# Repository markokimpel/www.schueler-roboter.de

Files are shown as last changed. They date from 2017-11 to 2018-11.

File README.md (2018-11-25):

---
permalink: /
---

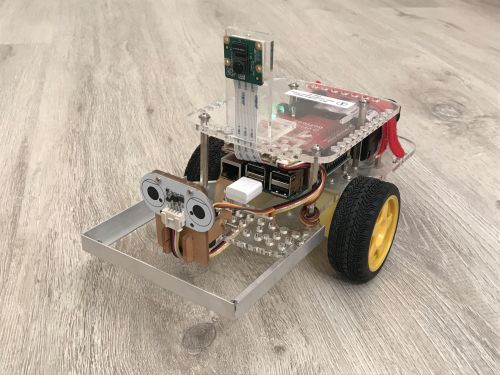
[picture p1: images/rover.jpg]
Schüler Roboter


* [Über das Projekt](project/)
* [News](news/)
  <ul>
    {% for post in site.posts %}
      <li>{{ post.date | date: "%d-%b-%Y" }} <a href="{{ post.url }}">{{ post.title }}</a></li>
      {% if forloop.index == 5 %}
        {% break %}
      {% endif %}
    {% endfor %}
  </ul>
* Anleitungen
  * [Bau des Roboters](tutorials/build_a_robot/)
  * [Basisinstallation Software](tutorials/software_image/)
  * [Programmieren mit Scratch](tutorials/programming_with_scratch/)
  * [Bilderkennung mit OpenCV](tutorials/image_recognition_with_opencv/)
* [Kontakt](contact/)

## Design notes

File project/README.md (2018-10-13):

---
title: Über das Projekt
permalink: /project/
breadcrumb_path: home
---

## Vision

Schaffung einer offenen und leistungsstarken Plattform auf der Schüler jeden Alters mit Freunde Computerkenntnisse erwerben können.

## Der Schüler-Roboter ist ein fahrbarer Roboter auf Basis des Raspberry Pis

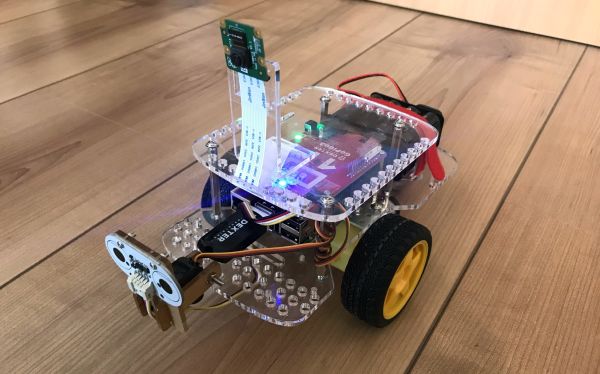
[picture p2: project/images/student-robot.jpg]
Schüler-Roboter


[Physical Computing](https://de.wikipedia.org/wiki/Physical_Computing) macht einfach mehr Spaß als das trockene Programmieren am Computer. Wir Menschen können leichter eine Verbindnung zu physischen Objekten aufbauen als zu abstrakten Aufgabenstellungen. Zielstellungen wie *Ding beweg dich* oder *mach' dies und das* ergeben sich bei physischen Objekten natürlich, ohne dass es einer zusätzlichen Motivation bedarf. Ein **selbstfahrender Roboter** erscheint hier als ideale Hardwarebasis.

Ein Raspberry Pi ist das Herzstück des Roboters. Der [Raspberry Pi 3 Model B](https://www.raspberrypi.org/products/raspberry-pi-3-model-b/) der Raspberry Pi Foundation ist ein leistungsstarker und kostengünstiger Einplatinenrechner. Seine offene Architektur erlaubt es verschiedene Betriebssysteme und Softwarepakete auf ihm laufen zu lassen und ihn mit verschiedenster Hardware zu integrieren. Seine große Beliebtheit im akademischen und Hobbybereich hat zu einer sehr aktiven Community und einem umfangreichen Angebot an Erweiterungen und Anleitungen geführt. Wir wählten den Raspberry Pi 3 Model B, da er ein **sehr breites Spektrum von Anwendungen** ermöglicht - von der Ansteuerung einzelner Komponenten (Motor an/aus), über die Programmierung mit Standardprogrammiersprachen wie Python, JavaScript und Java, die Nutzung von Roboterbetriebssystemen, bis zur Bilderkennung und künstlichen Intelligenz.

Als Hardwarebasis für den Roboter wird der [GoPiGo3](https://www.dexterindustries.com/gopigo3/) genutzt. Der GoPiGo3 ist einer der besten Roboter-Bausätze für den Raspberry Pi. Er enthält das Fahrgestell, die Motoren, Räder, die Steuerplatine, Stromversorgung, etc. Ein schwenkbarer Abstandssensor und eine leistungsstarke Kamera runden das Hardwarepaket ab.

## Ein sicherer Pfad durch den Jungle

Das umfangreiche und teilweise unübersichtliche Angebot an Komponenten und Software rund um den Raspberry Pi macht es dem Einsteiger bisweilen schwer geeignete und zueinander passende Komponenten auszuwählen und in ersten eigenen Projekten zu nutzen. Diese Hürde wird durch die **genaue Vorgabe von Komponenten** und **detailierten Anweisungen** genommen. Mit diesen erreichst du - mit Hilfe eines Kursleiters, Lehrers oder deiner Eltern - sicher das Ziel einen programmierbaren Roboters zu erschaffen. Die Programmierkurse sind auf diese Hardwarekomponenten abgestimmt. Von dem vorgegebenen Modell ausgehend können eigene Umbauten und Erweiterungen vorgenommen werden. Die Vielzahl der Projekte in der Community laden geradezu dazu ein.

## Einfach bis Rocket Science

Der Schüler-Roboter hat für jeden Schwierigkeitsgrad was zu bieten. Er eignet sich für Einsteiger, z.B. zum Erlernen der Programmierung mit der graphischen Programmiersprache Scratch. Er kann zum Erlernen von textuellen Programmiersprachen, wie z.B. Python, genutzt werden. Oder man taucht ein in die Bilderkennung und künstliche Intelligenz und lässt die neuesten Algorithmen auf ihm laufen.

## Alleine lernen oder in der Gruppe

Gerne kannst du dich allein durch die Anleitungen arbeiten. Oder du kommst du einer Veranstaltung. Interesse an einer massgeschneiderten Veranstaltung, z.B. für eine Schule? Bitte nehmen Sie [Kontakt](../contact/) mit uns auf.

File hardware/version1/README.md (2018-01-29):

[Hardware](..)

# Version 1

Version 1 nutzt ein selbstgedrucktes Chassis. Hierfür konnten wir freundlicherweise einen 3D Drucker der [Lichtwerkstatt](http://www.acp.uni-jena.de/lichtwerkstatt.html) des Abbe Center of Photonics nutzen. Es wird das gleiche Driver Board wie bei [Version 0](../version0/) verwendet. Die meisten der Kritikpunkte der Version 0 wurden durch die Eigenkonstruktion beseitigt. Zusätzlich wurde eine Kamera vorgesehen.

## Komponenten

Wir wählten folgende Komponenten:

Komponente | Bezug / Preis
-----------|------------
[Raspberry Pi 3 Model B](https://www.raspberrypi.org/products/raspberry-pi-3-model-b/) | [Amazon](https://www.amazon.de/gp/product/B01CD5VC92/) (ca. 35 €)
[Raspberry Pi Netzteil](https://www.raspberrypi.org/products/raspberry-pi-universal-power-supply/) | [Amazon](https://www.amazon.de/Raspberry-Offizielles-Pi-Netzteil-schwarz/dp/B01DP8O5A4/) (ca. 13 €)
32 GB microSD Karte mit Adapter<br/>(Kompatibilität mit Raspberry Pi beachten) | [Amazon](https://www.amazon.de/gp/product/B073JWXGNT/) (ca. 17 €)
[RapPiRobot Board V3](https://www.monkmakes.com/rrb3/) | (TODO)
[Raspberry Kamera](https://www.raspberrypi.org/products/camera-module-v2/) | (TODO)
2 Motoren und Räder | (TODO)
Nachlaufrad | (TODO)
2 Hülsen | (TODO)
3 Ultraschallsensoren | (TODO)
Steckbrett 400 Kontakte | (TODO)
Schrauben und Muttern | (TODO)
verschiedene Kabel | (TODO)
Batteriehalterung | (TODO)
6 AA Ni-MH Akkus mit hoher Kapazität | [Amazon](https://www.amazon.de/gp/product/B00JVV8HRW/) (2x ca. 12 €)
Ladegerät für AA Ni-MH Akkus | bereits vorhanden
**Gesamt** | **(TODO)**

PS: Die Auswahl der Komponenten basiert auf persönlichen Erfahrungen und Präferenzen. Bezugsquellen und Preise werden nur beispielhaft angegeben. Wir haben von keinem Hersteller oder Händler Vergünstigungen - jeglicher Art - für die Auswahl oder das Verlinken der Produkte erhalten.

## 3D Modell

* [Hauptplatte](3d_model/SR1%20Base%20Plate%20Rev%203.stl)
* [Raspberryhalterung](3d_model/SR1%20Raspberry%20Socket%20Rev%203.stl) (basiert auf [Raspberry Pi Case - HifiBerry Dac+](https://www.thingiverse.com/thing:2325301) von B_Dubb, veröffentlicht am 16. May 2017)
* [Abstandshalter Raspberryhalterung](3d_model/SR1%20Raspberry%20Socket%20Spacers%20Rev%201.stl)
* [Motorhalterung rechts](3d_model/SR1%20Motor%20Bracket%20R%20Rev%204.stl)
* [Motorhalterung links](3d_model/SR1%20Motor%20Bracket%20L%20Rev%204.stl)
* [Ultraschallsensorhalterung](3d_model/SR1%20Sonar%20Bracket%20Rev%202.stl) (3x benötigt)
* [Käfig mit Kamerahalterung](3d_model/SR1%20Cage%20Rev%200.stl)

Gedruckt wurde mit einem Prusa i3 MK2S, PLA, 200 µm.

## Fotos

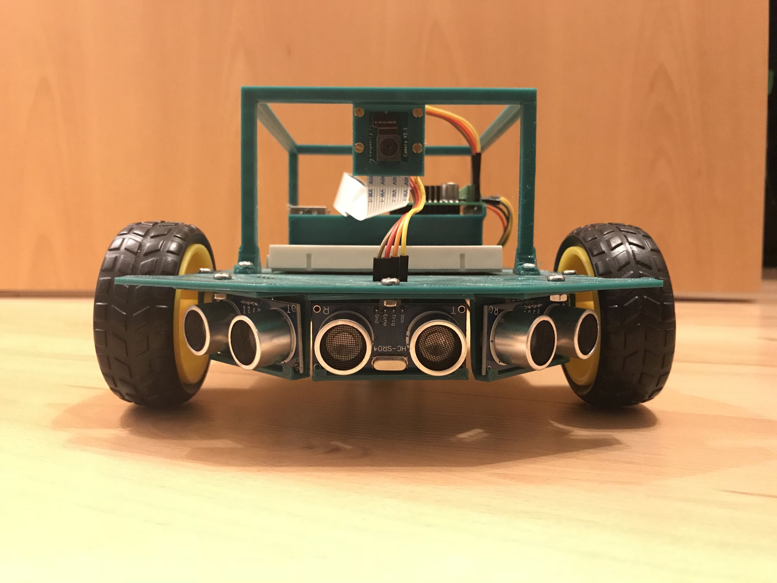
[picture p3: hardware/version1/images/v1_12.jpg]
vorn

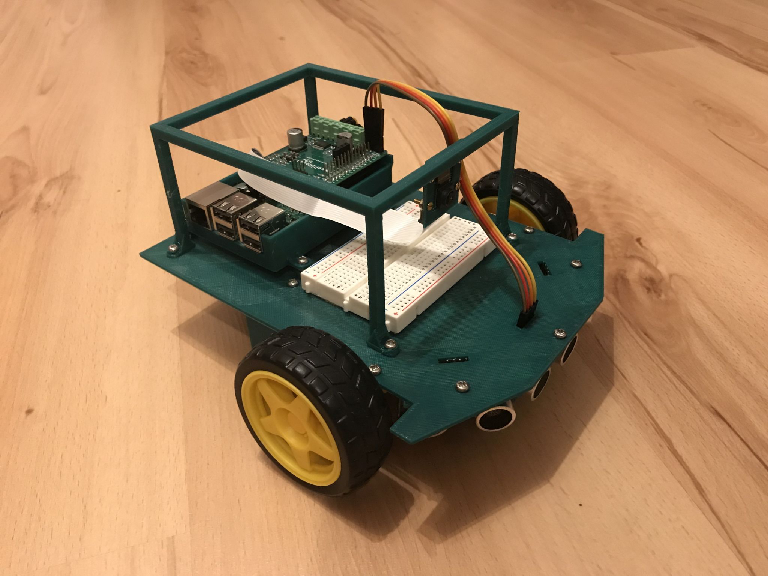
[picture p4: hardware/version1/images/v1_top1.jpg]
rechts

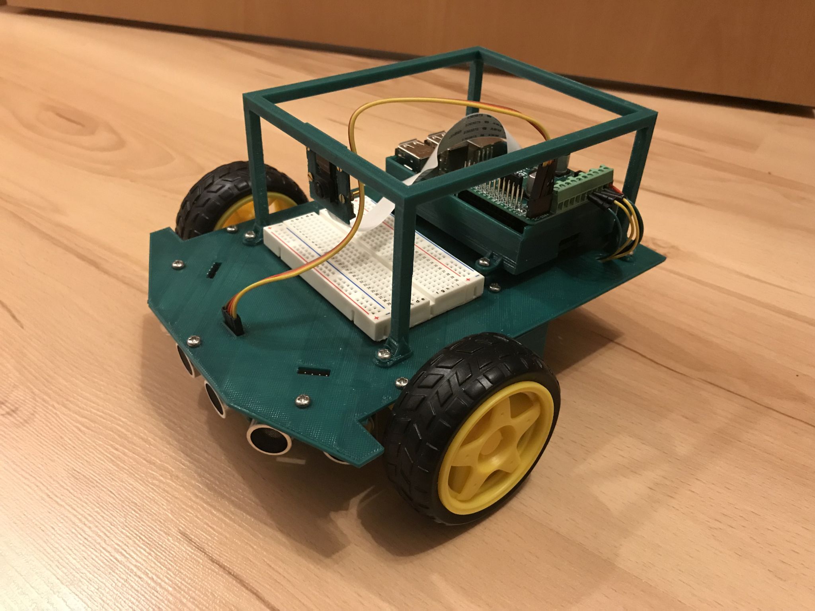
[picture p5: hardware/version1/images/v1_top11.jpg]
links

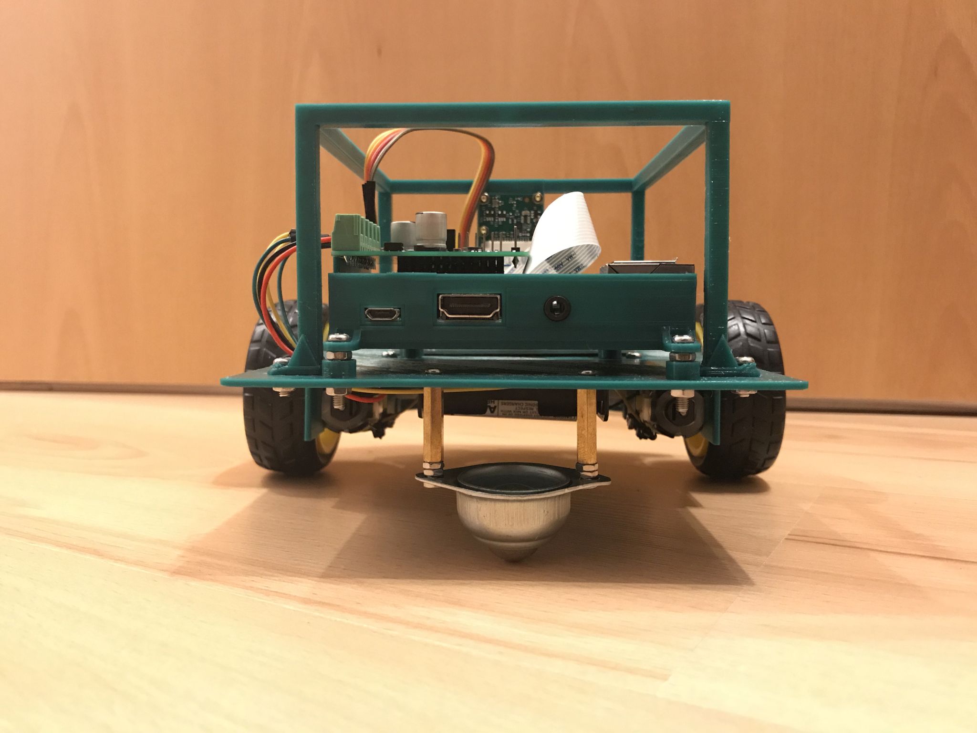
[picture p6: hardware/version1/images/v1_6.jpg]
hinten


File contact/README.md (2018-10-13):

---
title: Kontakt
permalink: /contact/
breadcrumb_path: home
---

Fragen? Anregungen? Du möchtest über zukünftige Veranstaltungen informiert werden? Sie sind an einer massgeschneiderten Veranstaltung interessiert?

Email: <a href="mailto:info@schueler-roboter.de">info@schueler-roboter.de</a>

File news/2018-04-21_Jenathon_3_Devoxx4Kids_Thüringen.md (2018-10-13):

---
title: 21-Apr-2018 Jenathon 3 / Devoxx4Kids Thüringen
breadcrumb_path: news
---

Der Schüler-Roboter war auf der [ersten Devoxx4Kids Thüringen Veranstaltung](https://www.meetup.com/jugthde/events/250002237/).

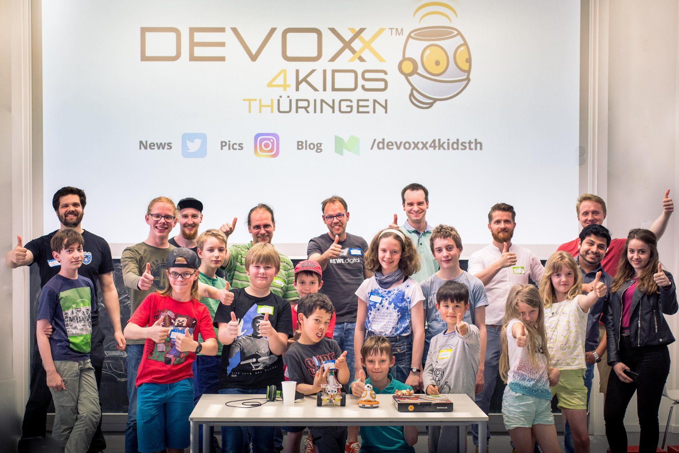
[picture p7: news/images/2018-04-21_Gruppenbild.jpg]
Gruppenbild

Foto: [Devoxx4Kids Thüringen](https://twitter.com/Devoxx4KidsTh/status/987843731784175616)

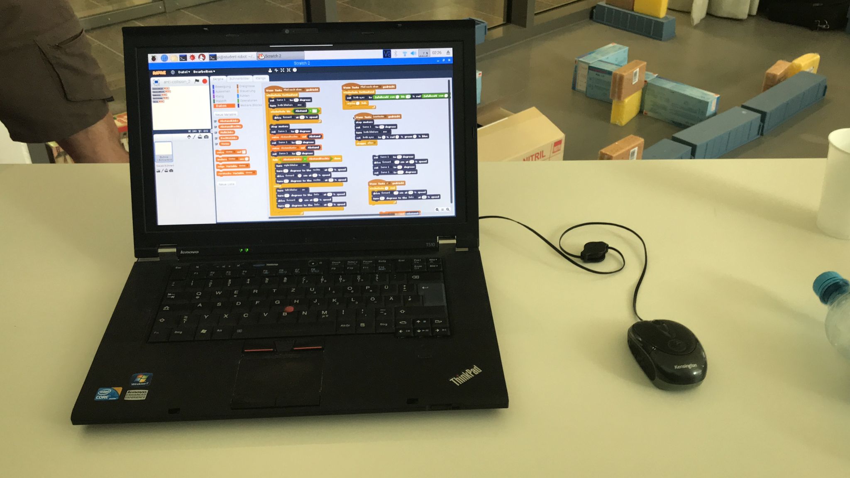
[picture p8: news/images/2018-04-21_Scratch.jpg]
Scratch


Schüler haben ein Scratch Programm geschrieben, dass den Roboter voll autonom durch ein Labyrinth fahren lässt.

Roboter in Labyrinth (https://youtu.be/aE33v_i1N6c)

Video: Robi im Labyrinth

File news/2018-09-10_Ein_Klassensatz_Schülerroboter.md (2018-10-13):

---
title: 10-Sep-2018 Ein Klassensatz Schüler-Roboter
breadcrumb_path: news
---

Dank der [Lichtwerkstatt](https://lichtwerkstatt-jena.de/) steht uns ein Klassensatz Schüler-Roboter zur Verfügung. Fertig zusammengebaut, mit dem neuesten Raspbian, Scratch, Python und OpenCV. Es kann los gehen!

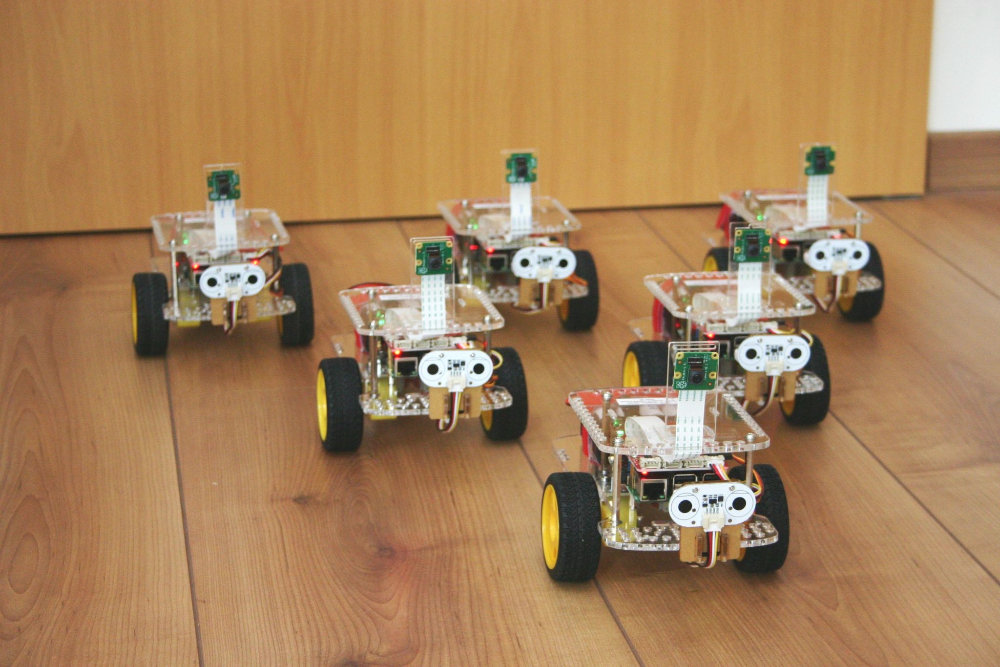
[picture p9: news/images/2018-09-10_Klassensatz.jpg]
Klassensatz Roboter


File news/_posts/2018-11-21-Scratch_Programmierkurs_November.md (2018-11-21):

---
title: Scratch Programmierkurs November
---

Der Scratch Programmierkurs im November bei Abantu hat großen Spaß gemacht. Großen Dank an die Jungs und Mädels, die voll dabei waren.

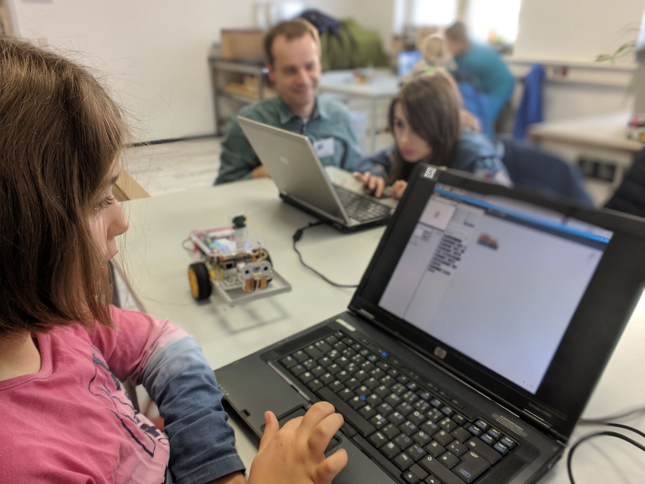
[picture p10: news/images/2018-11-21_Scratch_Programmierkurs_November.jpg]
Scratch Programmierkurs November


Roboter auf Fahrt (https://youtu.be/Kaua1VDBiig)

Video: Roboter auf Fahrt

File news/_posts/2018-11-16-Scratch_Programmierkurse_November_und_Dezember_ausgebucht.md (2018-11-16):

---
title: Scratch Programmierkurse November und Dezember ausgebucht
---

Die Scratch Programmierkurse im November und Dezember 2018 sind bereits ausgebucht. Weitere Kurse sind für nächstes Jahr geplant.

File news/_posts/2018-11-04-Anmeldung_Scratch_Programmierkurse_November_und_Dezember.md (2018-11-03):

---
title: Anmeldung Scratch Programmierkurse November und Dezember
---

Dieses Jahr gibt es noch zwei eintägige Scratch Programmierkurse mit dem Schüler-Roboter. Veranstalter ist das Abantu Kulturlabor. Details und Anmeldung gibt es [hier](https://www.facebook.com/abantu.kulturlabor/posts/1891471084240849).

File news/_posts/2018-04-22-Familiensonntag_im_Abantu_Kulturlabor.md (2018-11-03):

---
title: Familiensonntag im Abantu Kulturlabor
---

Roboter Programmierung für jedermann beim [Abantu Familiensonntag](https://www.facebook.com/abantu.kulturlabor/posts/1643032049084755).

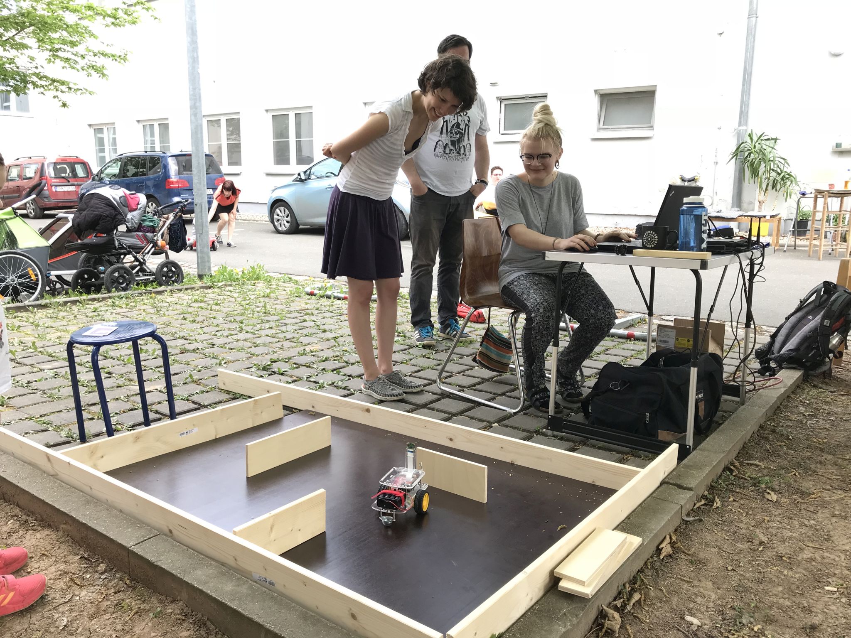
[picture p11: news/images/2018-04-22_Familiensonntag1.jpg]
Familiensonntag 1


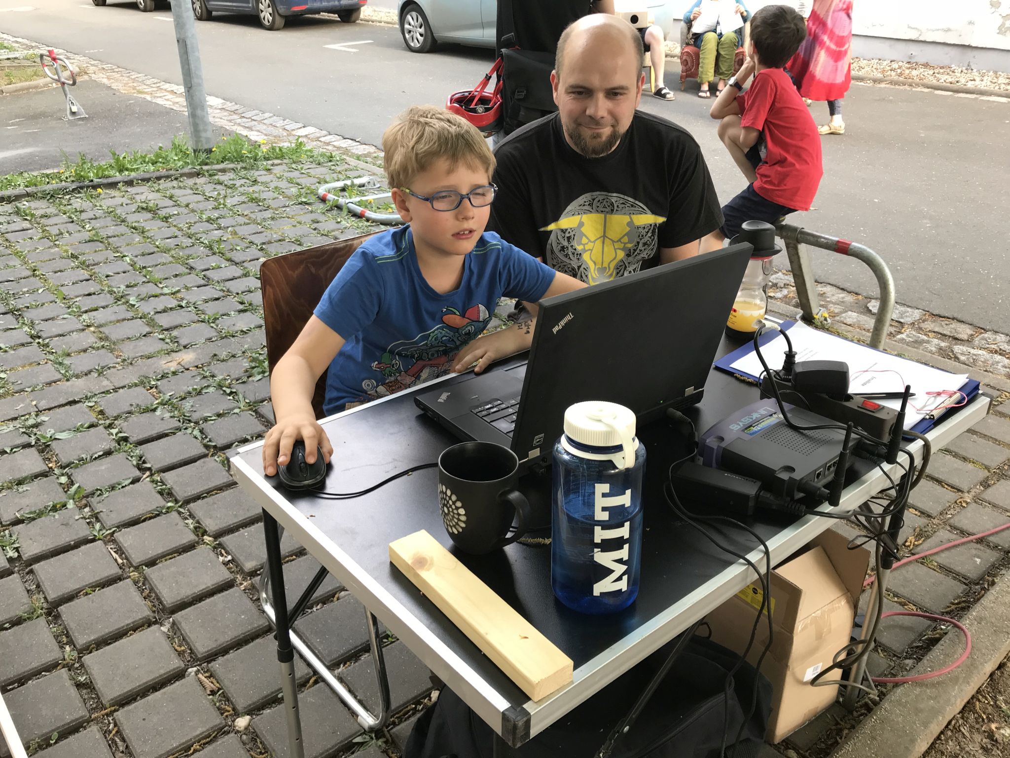
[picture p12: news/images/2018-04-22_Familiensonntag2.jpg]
Familiensonntag 2


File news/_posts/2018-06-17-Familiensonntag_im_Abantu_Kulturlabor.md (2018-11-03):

---
title: Familiensonntag im Abantu Kulturlabor
---

Der Schüler-Roboter mit dabei beim [Abantu Familiensonntag](https://www.facebook.com/abantu.kulturlabor/posts/1694381223949837).

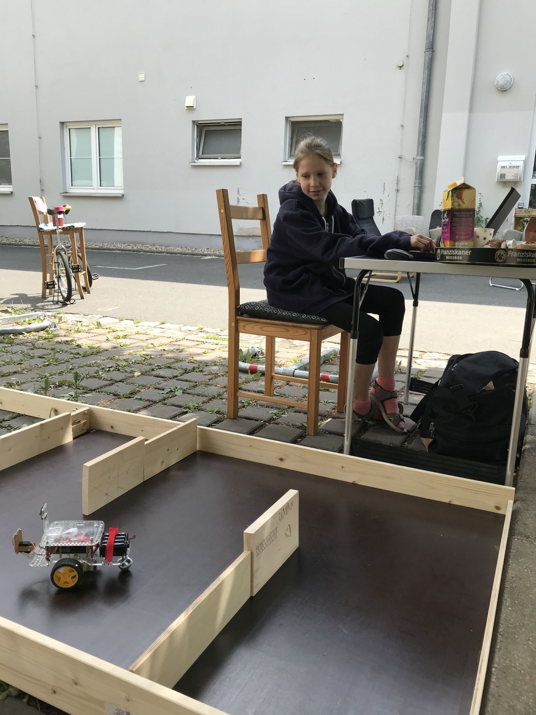
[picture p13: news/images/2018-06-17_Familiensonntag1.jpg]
Familiensonntag 1


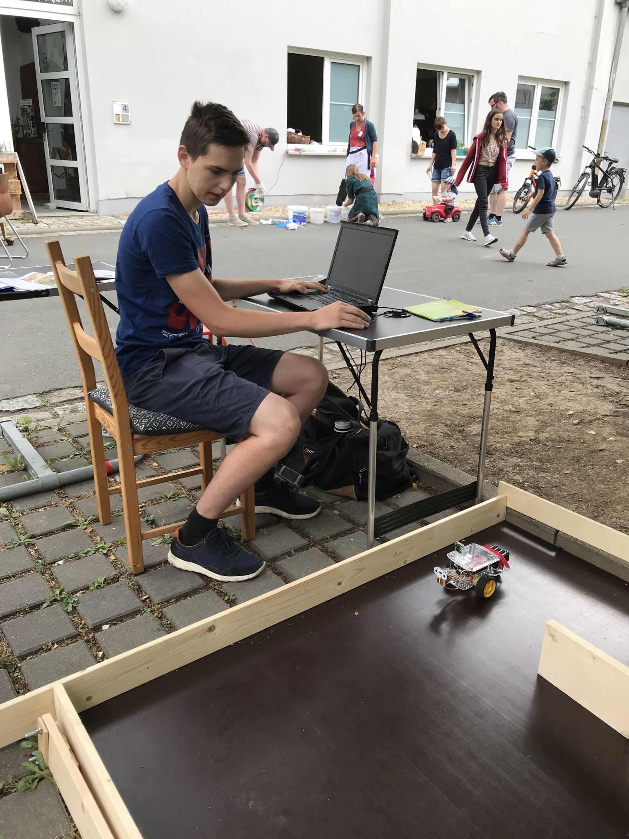
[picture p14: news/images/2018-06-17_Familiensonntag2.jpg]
Familiensonntag 2


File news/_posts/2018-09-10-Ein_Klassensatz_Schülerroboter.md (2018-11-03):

---
title: Ein Klassensatz Schüler-Roboter
---

Dank der [Lichtwerkstatt](https://lichtwerkstatt-jena.de/) steht uns ein Klassensatz Schüler-Roboter zur Verfügung. Fertig zusammengebaut, mit dem neuesten Raspbian, Scratch, Python und OpenCV. Es kann los gehen!

Klassensatz Roboter

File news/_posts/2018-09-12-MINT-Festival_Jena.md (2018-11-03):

---
title: MINT-Festival Jena
---

Auf dem [MINT-Festival Jena](https://www.mint.uni-jena.de/) waren wir mit einem Workshop vertreten. 12 Schüler der achten Klasse einer Gemeinschaftsschule aus Rudolstadt übten sich im Programmieren mit Scratch.

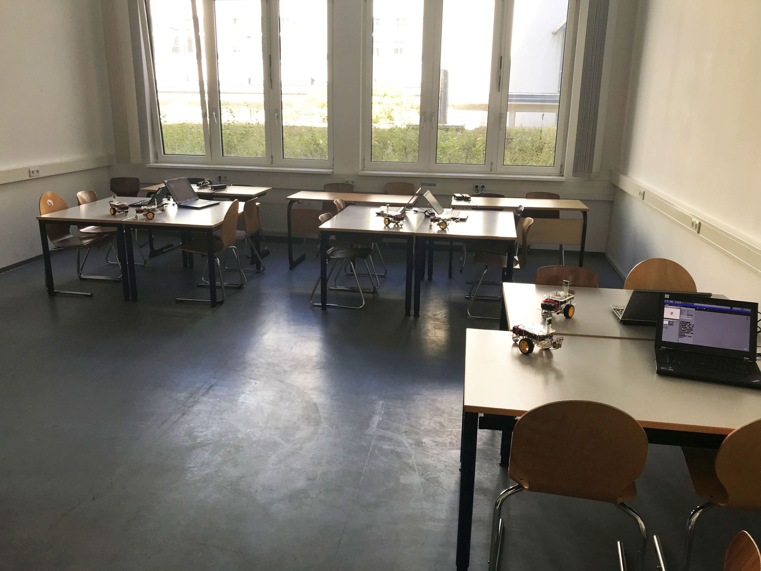
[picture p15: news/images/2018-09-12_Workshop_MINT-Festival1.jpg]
Workshop MINT-Festival


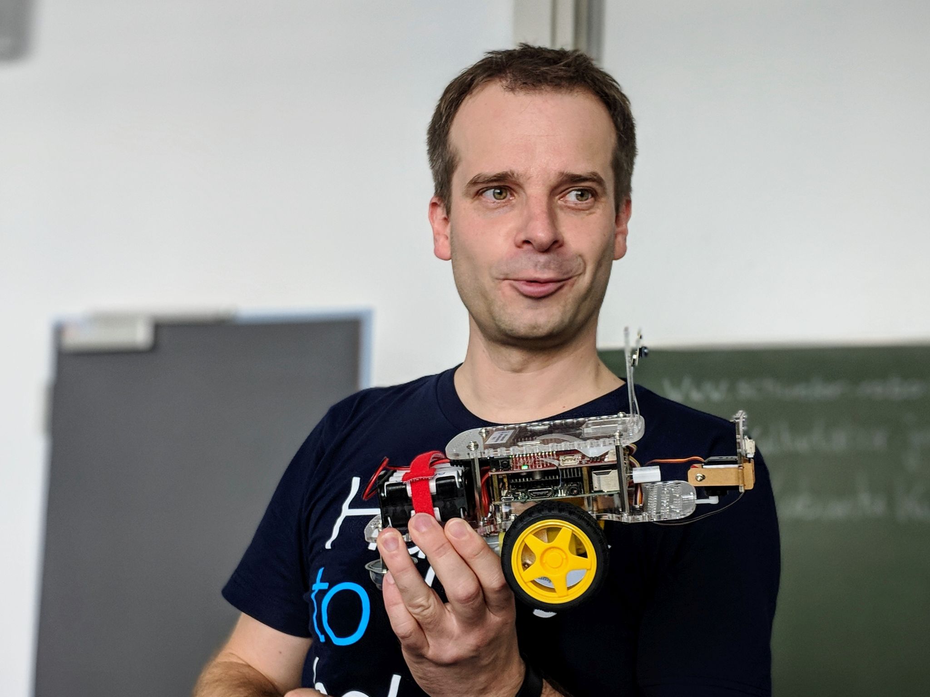
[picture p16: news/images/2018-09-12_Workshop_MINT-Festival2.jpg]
Workshop MINT-Festival

Foto: Maya

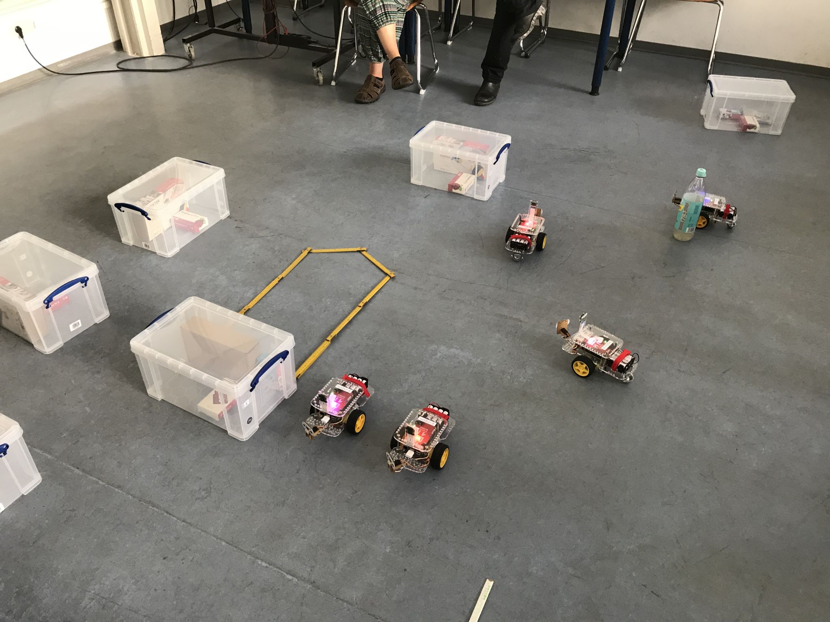
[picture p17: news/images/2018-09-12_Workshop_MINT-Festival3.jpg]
Workshop MINT-Festival


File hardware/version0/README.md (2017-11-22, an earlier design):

[Hardware](..)

# Version 0

Version 0 ist unser erster Wurf. Er basiert auf dem [RasPiRobot Rover Kit](https://www.monkmakes.com/pi-rover/) von [Monk Makes](https://www.monkmakes.com/). Dieses Kit hatte eine gute sehr gute [Kritik](https://www.raspberrypi.org/magpi/raspirobot-rover-kit-review/) vom MagPi Magazine bekommen.

## Komponenten

Wir wählten folgende Komponenten:

Komponente | Bezug / Preis
-----------|------------
[Raspberry Pi 3 Model B](https://www.raspberrypi.org/products/raspberry-pi-3-model-b/) | [Amazon](https://www.amazon.de/gp/product/B01CD5VC92/) (ca. 35 €)
[Raspberry Pi Netzteil](https://www.raspberrypi.org/products/raspberry-pi-universal-power-supply/) | [Amazon](https://www.amazon.de/Raspberry-Offizielles-Pi-Netzteil-schwarz/dp/B01DP8O5A4/) (ca. 13 €)
32 GB microSD Karte mit Adapter<br/>(Kompatibilität mit Raspberry Pi beachten) | [Amazon](https://www.amazon.de/gp/product/B073JWXGNT/) (ca. 17 €)
[RasPiRobot Rover Kit](https://www.monkmakes.com/pi-rover/) | [Amazon](https://www.amazon.de/gp/product/B018Y8IMUE/) (ca. 51 €)
6 AA Ni-MH Akkus mit hoher Kapazität | [Amazon](https://www.amazon.de/gp/product/B00JVV8HRW/) (2x ca. 12 €)
Ladegerät für AA Ni-MH Akkus | bereits vorhanden
**Gesamt** | **ca. 140 €**

PS: Die Auswahl der Komponenten basiert auf persönlichen Erfahrungen und Präferenzen. Bezugsquellen und Preise werden nur beispielhaft angegeben. Wir haben von keinem Hersteller oder Händler Vergünstigungen - jeglicher Art - für die Auswahl oder das Verlinken der Produkte erhalten.

## Kritik

### Gut

* Alles funktioniert!
* Das RasPiRobot Rover Kit ist recht umfangreich. Alle benötigten Teile - inkl. Schraubendreher in verschiedenen Größen - liegen bei. Der Zusammenbau per Anleitung ist gut möglich, wenn auch manchmal ein bisschen friemelig. Hilfe von Erwachsenen ist zwingend erforderlich.
* Das Driver Board [RasPiRobot Board V3](https://www.monkmakes.com/rrb3/) liegt dem RasPiRobot Rover Kit bei.
  * Die Stromversorgung des Raspberries erfolgt bei Batteriebetrieb über das Driver Board. Die gleiche Stromquelle (6x AA Batterien oder Akkus) kann für Raspberry (5V) und die Motoren (6V) genutzt werden.
  * Die beiden Motoren (rechts/links) werden über das Driver Board angesteuert. Jeweils sind vorwärts/rückwärts und verschiedene Geschwindigkeiten über PWM möglich.
  * Das Driver Board hat zusätzlich Anschlüsse für einen Ultraschall-Sensor (Sensor liegt dem Kit bei), zwei Schalter (eine Schalter liegt bei) und zwei Open Collector Ausgänge. Zwei LEDs sind verbaut und können über GPIO PINs angesprochen werden.
  * Das Glimmen der verbauten LEDs zeigt an, dass Raspi und Driver Board mit Batterie-Strom versorgt werden. (Da die rote LED des Raspis nur bei USB Strom leuchtet wüsste man sonst nicht, ob der Raspi mit Strom versorgt wird oder nicht.)
  * Beispielcode zum Ansteuern des verwendeten Driver Boards [RasPiRobot Board V3](https://www.monkmakes.com/rrb3/) mit Python liegt vor. Integration mit Scratch2 mit selbstgeschriebenem Code war möglich.
* Laufzeit mit Batterie/Akku ausreichend (mehrere Stunden).

### Verbessern

Bitte diese Kritikpunkte nicht als direkte Kritik am RasPiRobot Rover Kit misverstehen. Das Kit ist für verschiedene Nutzergruppen gedacht und die haben unterschiedliche Anforderungen. Hier geht es um Verbesserungen für den Schüler-Roboter.

* Ist der Raspi mit dem Chassis verschraubt, kommt man an viele Raspi Anschlüsse nur noch schwer ran: USB Stromversorgung - nur mit großer Vorsicht und kurzem Stecker, HDMI - nicht möglich, microSD Karte - schwierig und nur mit Hilfsmittel.
* Das Driver Board wird nur über die GPIO Kontakte des Raspis befestigt, d.h. an nur einer Seite. Schon leichte Stösse können die Kontakte beschädigen. 
* Dem Kit liegt ein Netzschalter bei. Um ihn zu benutzen müsste man aber löten. Alternativ wird der Raspi durch das Entfernen einer Batterie stromlos geschaltet. Funktioniert, ist aber nicht elegant. (Wohin legt man die verbleibende Batterie?)
* Häufig kam es zu Wackelkontakten im Batteriehalter. Die Suche nach dem Wackelkontakt war dann sehr schwierig. Ursache ist wahrscheinlich die Befestigung mit Schrauben. Die Schraubenköpfe sorgen bei der ersten und letzten Batterie für einen lockeren Sitz.
* Die Batterien/Akkus können nur schwer von Kindern eingelegt werden. Das Batterienfach befindet sich auf der Unterseite. Der Roboter kann nicht auf seine Oberseite gelegt werden - dann würden Ultraschall-Sensor oder Driver Board verbiegen. Kinder können den Roboter nicht in einer Hand halten und wenden - aufgrund seiner Größe müssten sie ihn an nur einer Ecke festhalten und dafür ist er zu schwer.
* Batterien waren für uns aufgrund des entstehenden Abfalls keine Option. Die 6 Ni-MH Akkus konnten jedoch nicht wirklich überzeugen. Ihre Kapazität 6x min. 2500mAh (bei 1,2V) war für den Betrieb völlig ausreichend. Die Ladezeit ist jedoch sehr lang: die meisten Ladegeräte können maximal 4 Akkus gleichzeitig laden. D.h. man benötigt zwei Durchläufe um 6 Akkus zu laden. Praktisch wird man sich ein zweites Pack an Akkus zulegen.
* Da es keine Ladestandsanzeige gibt, kann der Moment, an dem der Raspi plötzlich abstürzt nicht vorausgesagt werden. Ärgerlich, wenn man länger nicht gespeichert hat.

## Fotos

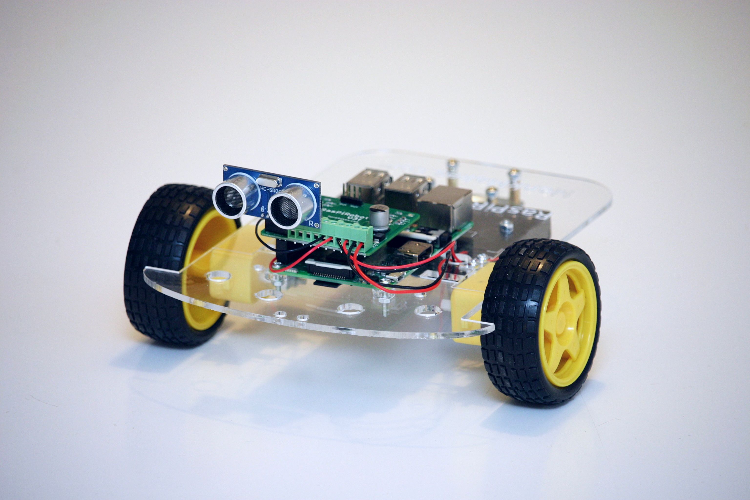
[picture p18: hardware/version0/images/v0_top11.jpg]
oben vorn

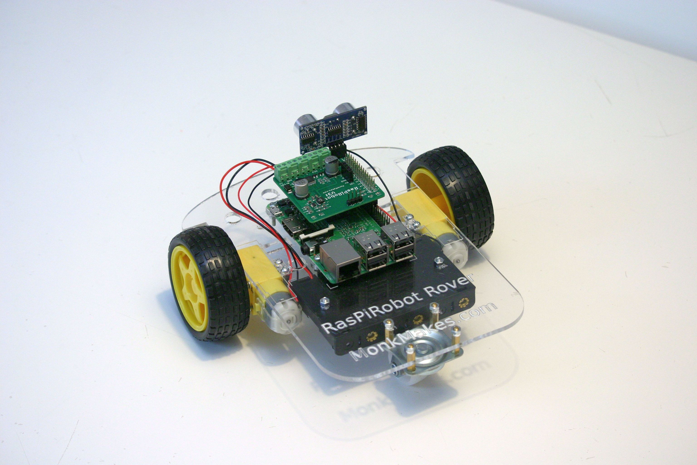
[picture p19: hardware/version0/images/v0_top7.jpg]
oben hinten

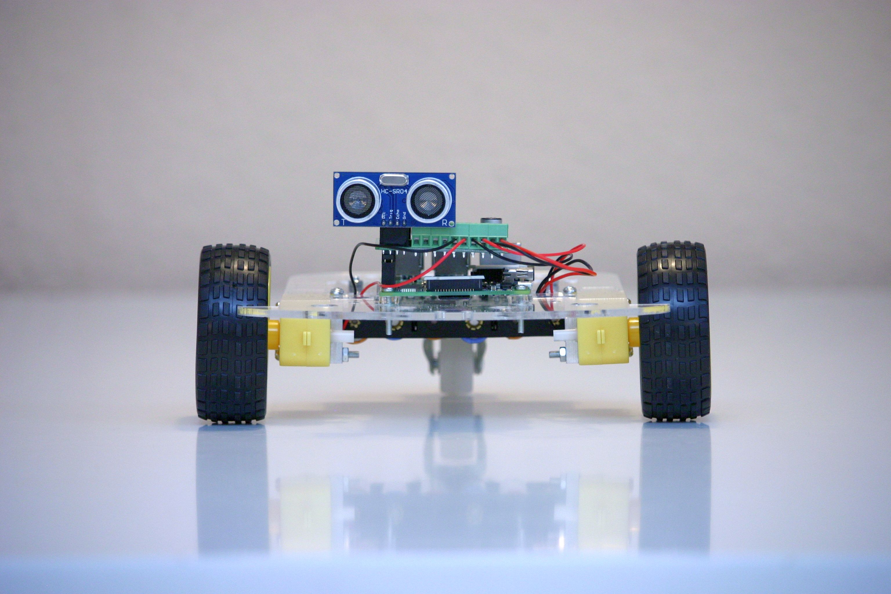
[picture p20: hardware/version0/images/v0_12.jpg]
vorn

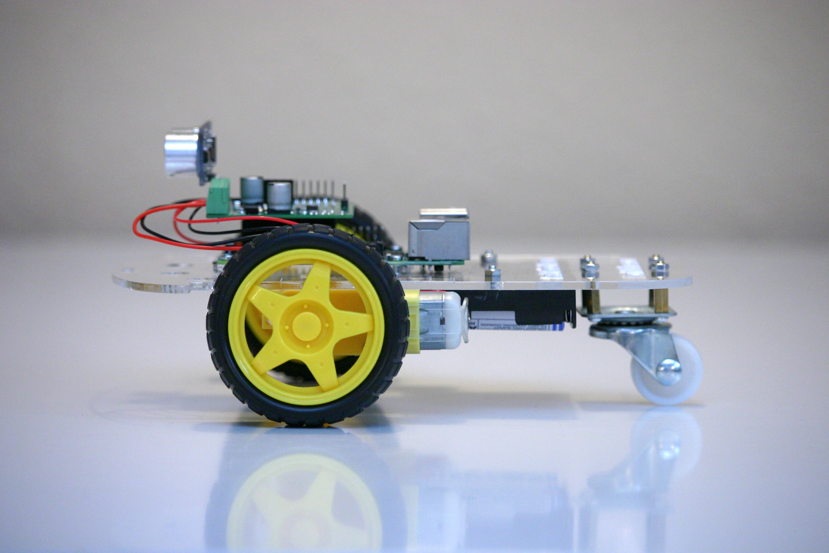
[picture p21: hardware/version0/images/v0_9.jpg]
seite

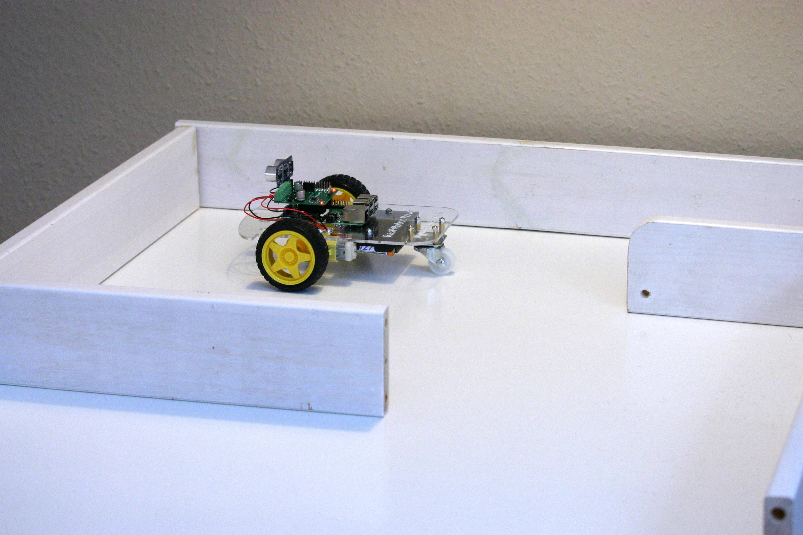
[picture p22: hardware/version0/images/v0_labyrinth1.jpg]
Labyrinth 1

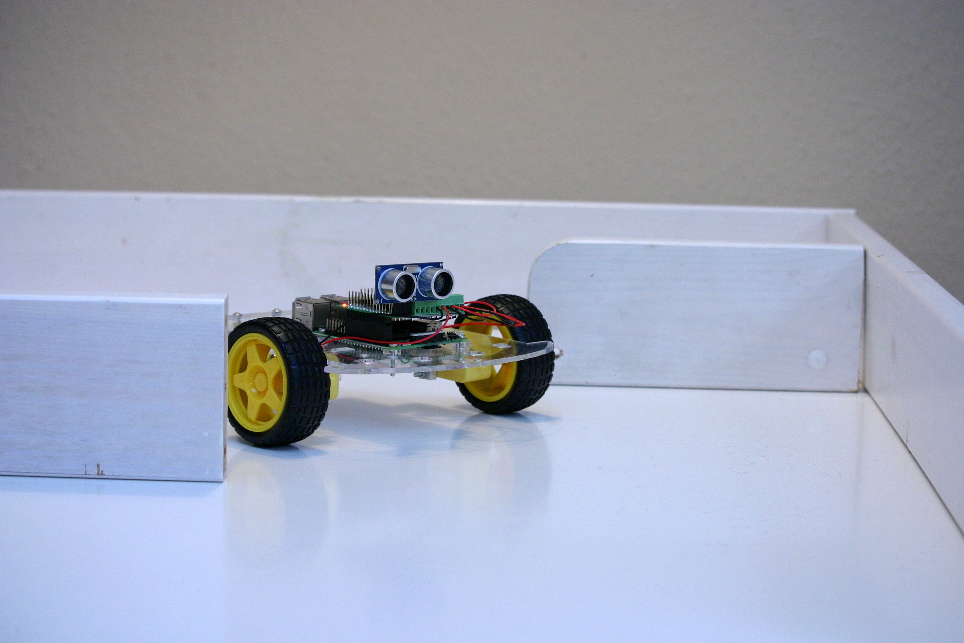
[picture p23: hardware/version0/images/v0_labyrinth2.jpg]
Labyrinth 2


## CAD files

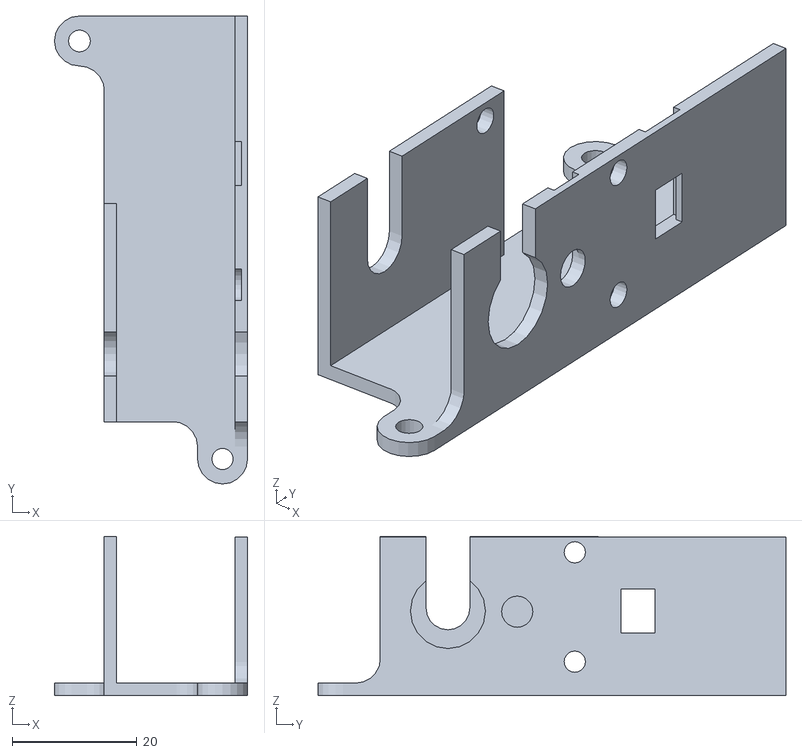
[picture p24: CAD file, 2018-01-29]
hardware/version1/3d_model/SR1 Motor Bracket R Rev 4.stl
30.9 x 74.9 x 25.5

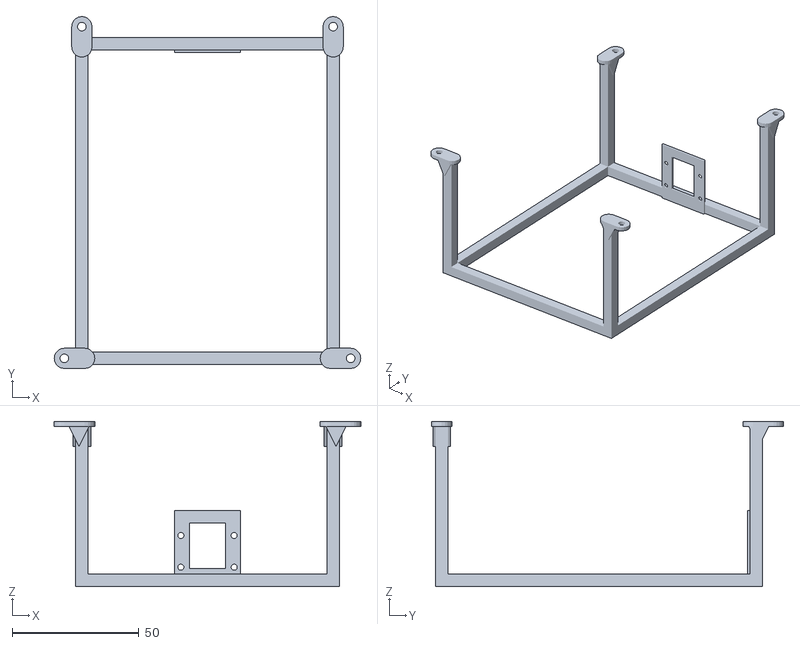
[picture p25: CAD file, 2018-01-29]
hardware/version1/3d_model/SR1 Cage Rev 0.stl
120.8 x 138.7 x 65.2

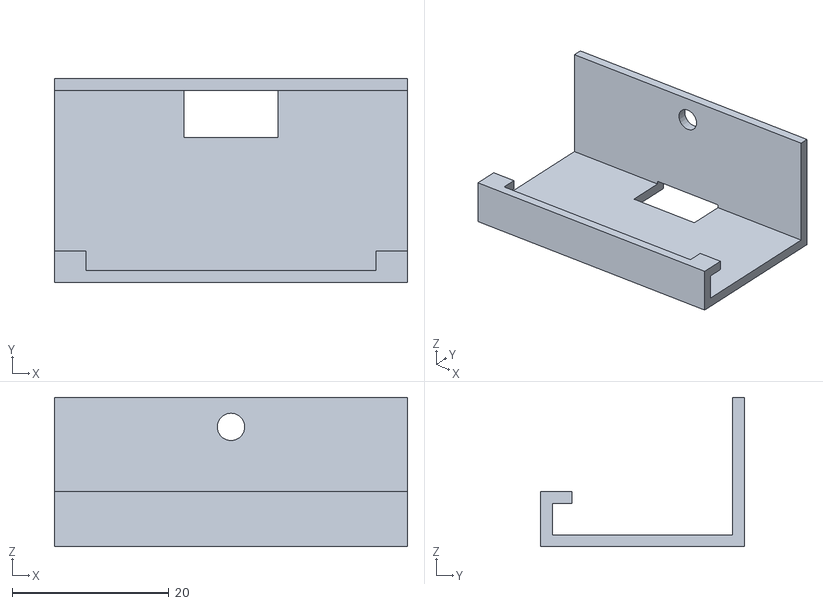
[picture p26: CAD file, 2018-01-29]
hardware/version1/3d_model/SR1 Sonar Bracket Rev 2.stl
45.0 x 26.0 x 19.0

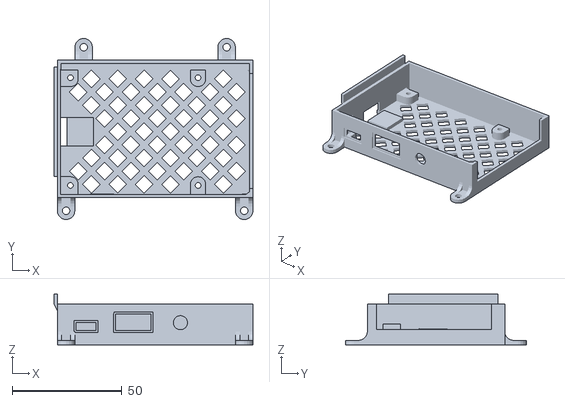
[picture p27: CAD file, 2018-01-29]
hardware/version1/3d_model/SR1 Raspberry Socket Rev 3.stl
90.5 x 82.4 x 23.0

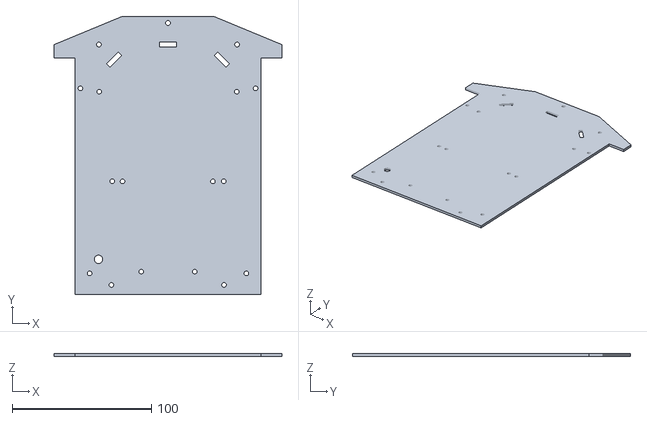
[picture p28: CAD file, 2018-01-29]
hardware/version1/3d_model/SR1 Base Plate Rev 3.stl
164.0 x 200.0 x 2.00

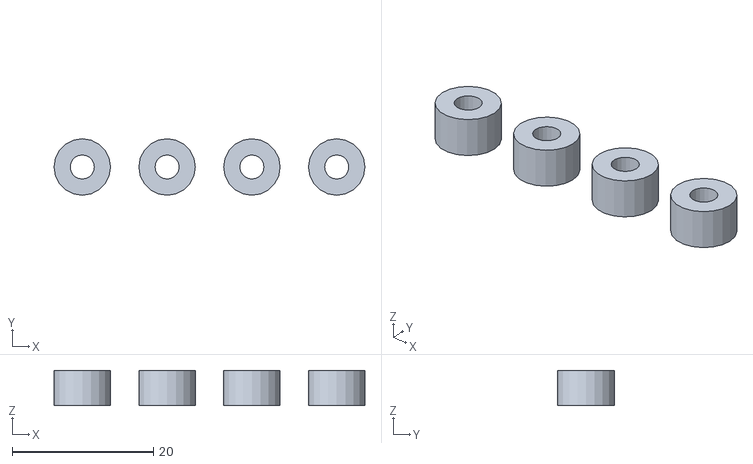
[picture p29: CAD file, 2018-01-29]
hardware/version1/3d_model/SR1 Raspberry Socket Spacers Rev 1.stl
44.0 x 8.00 x 5.00

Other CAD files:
hardware/version1/3d_model/SR1 Motor Bracket L Rev 4.stl

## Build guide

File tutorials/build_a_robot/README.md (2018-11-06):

---
title: Bau des Roboters
permalink: /tutorials/build_a_robot/
breadcrumb_path: home
---

## Komponenten

Komponente | Bezug / Preis
-----------|------------
[GoPiGo3 Robot Base Kit](https://www.dexterindustries.com/shop/gopigo3-robot-base-kit/) | [Génération Robots](https://www.generationrobots.com/de/402746-gopigo-base-kit.html) (ca. 107 €)
[Servo Set](https://www.dexterindustries.com/shop/servo-package/) | [Génération Robots](https://www.generationrobots.com/de/401931-servoset-fuer-den-robotikkit-gopigo.html) (ca. 16 €)
[Entfernungssensor](https://www.dexterindustries.com/shop/distance-sensor/) | [Génération Robots](https://www.generationrobots.com/de/402750-laserscanner-gopigo-kompatibel.html) (ca. 21 €)
[Befestigungswinkel für Kamera](https://www.dexterindustries.com/shop/acrylic-sensor-mounts-set-of-4/) | [Génération Robots](https://www.generationrobots.com/de/402749-acryl-halter-fur-gopigo-sensoren.html) (ca. 17 €)
[Raspberry Pi 3 Model B](https://www.raspberrypi.org/products/raspberry-pi-3-model-b/) | [Amazon](https://www.amazon.de/gp/product/B01CD5VC92/) (ca. 30 €)
32 GB microSD Karte mit Adapter<br/>(Kompatibilität mit Raspberry Pi beachten) | [Amazon](https://www.amazon.de/gp/product/B06XFSZGCC/) (ca. 8 €)
[Raspberry Pi USB WiFi Dongle](https://www.raspberrypi.org/products/raspberry-pi-usb-wifi-dongle/) | [Reichelt](https://www.reichelt.de/raspberry-pi-usb-wifi-dongle-150-mbit-s-raspberrypi-wifi-p161090.html) (ca. 12 €)
[Raspberry Pi Camera Module v2](https://www.raspberrypi.org/products/camera-module-v2/) | [Amazon](https://www.amazon.de/Raspberry-Pi-V2-1-1080P-Kamera-Modul/dp/B01ER2SKFS/) (ca. 19 €)
[Raspberry Pi Netzteil](https://www.raspberrypi.org/products/raspberry-pi-universal-power-supply/) | [Amazon](https://www.amazon.de/Raspberry-Offizielles-Pi-Netzteil-schwarz/dp/B01DP8O5A4/) (ca. 13 €)
8 AA Ni-MH Akkus mit hoher Kapazität | [Amazon](https://www.amazon.de/gp/product/B00JVV8HRW/) (2x ca. 12 €)
Ladegerät für AA Ni-MH Akkus | bereits vorhanden
Stoßstange | [OBI](https://www.obi.de/profile/ba-profil-winkel-gleichschenklig-natur-10-mm-x-10-mm-x-1000-mm/p/3325198) (ca. 2 €)
Aufbewahrungsbox | [Böttcher](https://www.bueromarkt-ag.de/aufbewahrungsbox_really-useful-box_14c_14l,p-rub-14c.html) (ca. 14 €)
**Gesamt** | **ca. 283 €**

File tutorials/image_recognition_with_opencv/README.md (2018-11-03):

---
title: Bilderkennung mit OpenCV
permalink: /tutorials/image_recognition_with_opencv/
breadcrumb_path: home
---

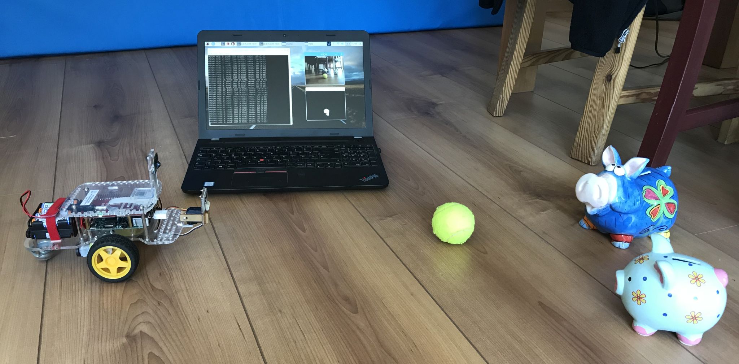
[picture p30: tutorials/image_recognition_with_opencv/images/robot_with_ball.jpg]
Roboter mit Ball


## Voraussetzungen

* Roboter mit der aktuellen Software (siehe [Bau des Roboters](../build_a_robot/) und [Basisinstallation Software](../software_image/)) zuzüglich Installation von OpenCV und Numpy.
* Python Programmierkenntnisse
* Einen weiteren Computer um auf den Roboter zuzugreifen. An diesem Computer sitzt du und programmierst den Roboter. Der Computer kann ein Raspberry Pi mit Monitor, Tastatur und Maus sein, oder ein Windows Laptop. Da der Roboter über WLAN kommuniziert, muss auch der weitere Computer über WLAN kommunizieren können.
* Wie du den Roboter an- und ausschaltest und dich mit dem VNC Viewer und mit ssh verbindest ist in [Mit Roboter verbinden](../software_image/#mit-roboter-verbinden) und [Roboter ausschalten](../software_image/#roboter-ausschalten) erklärt.

## Aufgabe

Ein Objekt, z.B. Tennisball, soll aufgrund seiner Farbe erkannt werden. Der Roboter passt seine Blickrichtung zum Objekt hin an. Er folgt dem Objekt.

## Lösungsidee

Mit der Kamera werden ständig Bilder aufnommen. Mit OpenCV wird nach den Farbwerten des gesuchten Objekts gefiltert. Das Objekt wird dort vermutet, wo es besonders viele Bildpunkte mit passender Farbe gibt. In diese Richtung dreht sich der Roboter.

## Lösungsbeispiel

```python
import time

from pivideocapture import PiVideoCapture

import cv2
import numpy as np

from easygopigo3 import EasyGoPiGo3

with PiVideoCapture(resolution=(320,240), framerate=10) as vc:
    
    print("camera resolution: {}".format(vc.camera_resolution()))
    print("camera framerate : {}".format(vc.camera_framerate()))

    egpg3 = EasyGoPiGo3()
    try:
        # move distance sensor straight (just to look nice)
        egpg3.init_servo(port = "SERVO1").reset_servo()

        print("Press Ctrl-C to stop")
        try:
            while True:
                original = vc.read()
                hsv = cv2.cvtColor(original, cv2.COLOR_BGR2HSV)
                #print("hsv: {0[0]} {0[1]} {0[2]}".format(hsv[0,0]))
                mask = cv2.inRange(hsv, np.array([20,100,70]), np.array([40,255,255]))
                
                cv2.imshow('original', original)
                #cv2.imshow('hsv', hsv)
                cv2.imshow('mask', mask)

                cv2.waitKey(1)

                # each mask element contains the values 0 or 255
                # sum up matching pixels per column
                match_distribution = mask.sum(axis=0) // 255
                total_matches = match_distribution.sum()
                matches = total_matches / mask.size

                if matches > 0.002:
                    sum = 0
                    for i in range(match_distribution.size):
                        sum += i * match_distribution[i]

                    average = sum // total_matches
                    match_center = average / match_distribution.size

                    print("matches col0: {}, total: {} ({:.4f}), center: {} ({:.2f})". \
                        format(match_distribution[0], total_matches, matches, average, match_center))

                    if match_center < 0.45:
                        egpg3.set_speed(egpg3.DEFAULT_SPEED * ((0.5 - match_center) * 1.5))
                        egpg3.spin_left()
                    elif match_center < 0.55:
                        egpg3.stop()
                    else:
                        egpg3.set_speed(egpg3.DEFAULT_SPEED * ((match_center - 0.5) * 1.5))
                        egpg3.spin_right()

                else:
                    print("matches col0: {}, total: {} ({:.4f})". \
                        format(match_distribution[0], total_matches, matches))
                    egpg3.stop()

        except KeyboardInterrupt:
            pass

    finally:
        egpg3.reset_all()

    print("elasped time: {:.2f} secs".format(vc.elapsed_time()))
    print("capture rate: {:.2f} fps".format(vc.capture_framerate()))
    print("drop rate   : {:.2f} fps".format(vc.drop_framerate()))
```

Rechts oben das Originalbild von der Kamera. Das untere Bild zeigt Stellen mit grünlichen Farben weiss an. Dort wird der Ball vermutet.

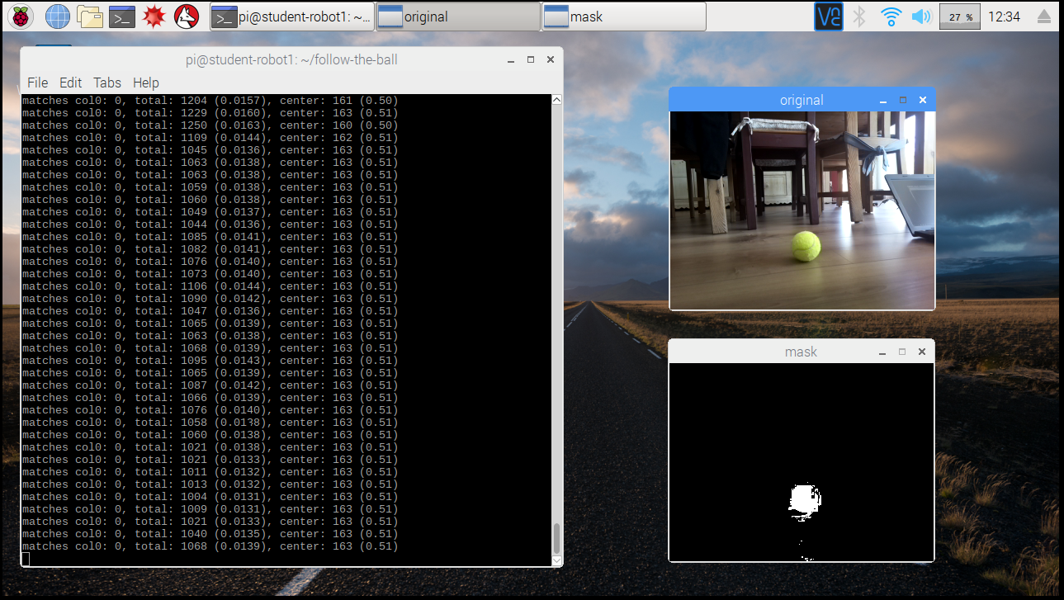
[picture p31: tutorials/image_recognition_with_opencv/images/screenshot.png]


Filtern der Kamerabilder nach grünlichen Farben:

Objekterkennung durch Filtern nach Farben 1/2 (https://youtu.be/Yp2DmdV0uzA)

Der Roboter bewegt sich in die Richtung mit den meisten passenden Farben:

Objekterkennung durch Filtern nach Farben 2/2 (https://youtu.be/Bk6Mf2Azcjs)

*Copyright 2018 Marko Kimpel*

*Licensed under the GNU General Public License version 3, or (at your option) any later version.*

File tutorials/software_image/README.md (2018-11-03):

---
title: Basisinstallation Software
permalink: /tutorials/software_image/
breadcrumb_path: home
show_toc: true
toc_h_max: 3
---

## Die Schüler-Roboter Softwareinstallation

Der Roboter nutzt einen Raspberry Pi 3 Model B als Herzstück. Das Standard-Betriebssystem für den Raspberry Pi ist [Raspbian](https://de.wikipedia.org/wiki/Raspberry_Pi#Raspbian). Es gibt aber auch Alternativen. Beispielsweise bietet Dexter Industries für den GoPiGo3 [DexterOS](https://www.dexterindustries.com/dexteros/get-dexteros-operating-system-for-raspberry-pi-robotics/), [Raspbian for Robots](https://www.dexterindustries.com/raspberry-pi-robot-software/) und [Cinch](https://www.dexterindustries.com/howto/use-cinch-operating-system/) an. DexterOS ist leicht zu benutzen und zu updaten, beinhaltet eine Scratch-ähnliche Umgebung namens Bloxter ([Onlineversion](http://www.bloxter.com/)) und eine Entwicklungsumgebung für Python. DexterOS ist Closed Source und nicht erweiterbar - kein freier Zugriff auf das Dateisystem, keine Installation eigener Software. Raspbian for Robots basiert auf Raspbian, mit zusätzlicher Software von Dexter Industries. Cinch soll das Erstellen eines Wi-Fi Access Points ermöglichen.

Für die Experimente mit dem Schüler-Roboter wird eine eigene Softwareinstallation benutzt:
* Basis ist ein aktuelles Raspbian.
* Mit Bibliotheken um den GoPiGo3 anzusteuern.
* Sie enthält weitere Software für die Workshops, z.B. Integration mit Scratch 2 Offline Editor und ScratchX.
* Der im GoPiGo3 verbaute Raspberry Pi muss nicht mit Tastatur, Maus oder Bildschirm verbunden werden - er wird *headless* betrieben.
* Funktionen zum Aktualisieren und Zurücksetzen der Installation.
* Die SD Karte muss für Aktualisierungen und zum Zurücksetzen der Installation nicht entfernt werden.
* Automatische Erstellung eines Wi-Fi Access Points zum leichten kabellosen Verbinden mit dem Roboter. Ein WLAN wird nicht benötigt.
* Zusätzlich kann sich der Roboter über einen USB WLAN Adapter mit dem lokalen WLAN verbinden. Damit sind die Nutzung des Access Points und Internet gleichzeitig möglich.

Wer es einfach mag, nutzt ein vorhandenes Kartenimage und muss sich um die Details der Installation und Konfiguration nicht kümmern. Siehe Kapitel [SD Karte initial beschreiben](#sd-karte-initial-beschreiben) und [Mit Roboter verbinden](#mit-roboter-verbinden). Gruppenleiter sollten ausserdem [Installation anpassen](#installation-anpassen) und [Installation zurücksetzen](#installation-zurücksetzen) lesen. In [SD Karte aktualisieren](#sd-karte-aktualisieren) ist beschrieben, wie die Installation ohne das Entfernen der SD Karte aktualisiert werden kann. [SD Kartenimage erstellen](#sd-kartenimage-erstellen) ist für die Maintainer des Kartenimages und technisch Interessierte gedacht.

## SD Karte initial beschreiben

Um die SD Karte im GoPiGo3 zu wechseln, müssen mehrere Kabel entfernt werden. Das ist mühsam und tut den Steckverbindern auch nicht gut. Deshalb versuchen wir die Karte so selten wie möglich zu wechseln. Am Besten du beschreibst die Karte vor dem Bau des Roboters und steckst sie in den Raspberry Pi. Spätere Aktualisierungen von RaspbianForStudentRobot sind in der Regel ohne das Entfernen der Karte möglich.

Zum initialen Beschreiben der SD Karte brauchst du einen weiteren Computer mit SD Kartenleser, z.B. einen Windows Laptop. Die physische Kartengröße muss microSD sein, denn nur diese akzeptiert der Raspberry Pi 3 Model B. Wir empfehlen eine Kapazität von 32 GB. Häufig werden microSD Karten mit einem Adapter verkauft. Mit diesem können sie in einem Computer genutzt werden, der nur die SD Größe unterstützt.

Die SD Karte muss eine Partition haben und diese muss mit FAT32 formatiert sein. Das ist bei neue gekauften Karten in der Regel bereits der Fall. Ansonsten kann das mit Betriebssystem Boardmitteln erreicht werden, oder du nutzt den [SD Memory Card Formatter](https://www.sdcard.org/downloads/formatter_4/index.html) der [SD Association](https://www.sdcard.org/).

RaspbianForStudentRobot liegt als zip Datei vor. Den Inhalt der Datei musst du auf die SD Karte kopieren.

Dann stecke die Karte in den Raspberry Pi und baue den Roboter fertig zusammen.

Ist der Roboter fertig zusammengebaut, die Kamera, der Servo, der Abstandssensor und der Wi-Fi Adapter installiert, kannst du den Roboter erstmalig starten. Das machst du, indem du die Power Taste (rechts hinten am GoPiGo3 Board) drückst. Beim ersten Start wird das Betriebssystem automatisch installiert und dann gestartet. Während dieses Vorgangs blinkt die grüne LED neben der Power Taste. Die kleine grüne LED neben dem mini-USB Anschluss blinkt bei Lese- und Schreiboperationen auf der SD Karte. Die Zeitdauer für die Installation hängt von der Geschwindigkeit der SD Karte ab. Bei einer 32 GB Samsung EVO Plus dauert die Installation etwa 12 Minuten. Die Installation ist abgeschlossen und das Betriebssystem gestartet, wenn die LED neben der Power Taste ständig grün leuchtet. Jetzt kannst du dich mit dem Roboter verbinden - siehe unten.

## Mit Roboter verbinden

* Arbeitsrechner mit WLAN
  * Du brauchst einen weiteren Computer um auf den Roboter zuzugreifen. An diesem Arbeitsrechner sitzt du und programmierst den Roboter. Der Arbeitsrechner kann ein Raspberry Pi mit Monitor, Tastatur und Maus sein, oder ein Windows Laptop. Da der Roboter über WLAN kommuniziert, muss auch der Arbeitsrechner über WLAN kommunizieren können.
* Roboter anschalten
  * Starte den Roboter indem du die Power Taste (rechts hinten am GoPiGo3 Board) drückst. Die grüne LED daneben beginnt zu blinken. Das bedeutet, das Betriebssystem wird geladen. Wenn die LED ständig grün leuchtet ist der Roboter betriebsbereit.
  * Übrigens: Wenn die LED neben der Power Taste beginnt gelb oder gar violett zu leuchten, dann bedeutet das die Akkus sind fast leer. Dann den Roboter ausschalten und Akkus wechseln.
* Arbeitsrechner mit Roboter WLAN verbinden
  * Der Roboter bietet ein WLAN Netzwerk an. Der Netzwerkname (SSID) ist *student-robot*, bei Arbeitsgruppen *student-robot[zahl]*. Das voreingestellte Passwort ist *changeitnow*. Bei Arbeitsgruppen erfrage das Passwort von deinem Gruppenleiter.
  * Verbinde dich mit deinem Arbeitsrechner zum WLAN des Roboters. Wennn du dich mit dem Roboter WLAN verbindest, verlierst du eine evtl. vorher bestehende WLAN Verbindung zum lokalen WLAN Router und damit zum Internet. Hierfür gibt es eine Lösung - siehe unten.
* Mit VNC Viewer am Roboter arbeiten
  * Mit dem VNC Viewer verbindest du dich zum Roboter und kannst den Desktop des Roboters sehen.
  * Bei Raspbian wird der VNC Viewer nicht mehr vorinstalliert. Er muss mit `sudo apt install realvnc-vnc-viewer` installiert werden. Die Verknüpfung befindet sich dann unter dem Menüpunkt *Internet*.
  * Für Windows kann der Viewer von [https://www.realvnc.com/de/connect/download/viewer/](https://www.realvnc.com/de/connect/download/viewer/) (Standalone EXE ist ausreichend) heruntergeladen werden.
  * Server-Adresse ist *student-robot.home*, bei Arbeitsgruppen *student-robot[zahl].home*. Beim ersten Aufruf muss die Identität des Servers bestätigt werden. Benutzname ist *pi*, das Passwort ist *myr0bot*.
  * Nun kannst du mit dem Raspbian Betriebssystem auf dem Roboter so arbeiten, als säßest du direkt davor.
* Roboter WLAN Passwort und Nutzerpasswort ändern
  * TODO
* Roboter mit dem lokalem WLAN verbinden
  * Wahrscheinlich war dein Arbeitsrechner über ein lokales WLAN mit dem Internet verbunden. Seitdem du dich mit dem Roboter WLAN verbunden hast, hat dein Arbeitsrechner keinen Internetzugriff mehr. Aber es gibt eine Lösung: Der Roboter hat zwei WLAN Schnittstellen. Die eine stellt das Roboter WLAN Netzwerk zur Verfügung und die andere kannst du mit dem lokalen WLAN verbinden. Dann haben dein Roboter, und über den Roboter auch dein Arbeitsrechner wieder Internetgriff.
  * Achtung: Ist der Roboter mit dem lokalem WLAN verbunden, können auch andere Nutzer des WLANs auf Dienste des Roboters zugreifen. Du solltest dich deshalb nur mit vertrauenswürdigen WLANs verbinden.
  * Am einfachsten richtest du die WLAN Verbindung vom Raspbian Desktop aus ein. Rechts oben in der Leiste ist das Symbol für WLAN. Dort wählst du das lokale WLAN Netzwerk aus und kannst dann das Passwort eingeben.
* Mit ssh auf Roboter zugreifen
  * Du kannst dich mit einem Terminal wie ssh oder PuTTY zur Kommandozeile des Roboters verbinden.
  * Die Adresse ist *student-robot.home*, Nutzername *pi* und Passwort *myr0bot*. Beim ersten Verbinden muss die Signatur des Servers bestätigt werden.

## Roboter ausschalten

* Das geht einfach: Offene Dokumente speichern, dann die Power Taste (rechts hinten am GoPiGo3 Board) drücken. Die LED daneben beginnt rot zu blinken. Offene Programme werden beendet und das Betriebssystem wird heruntergefahren. Die LED geht aus, wenn der Roboter vollständig heruntergefahren wurde. Du kannst nun die Akkus entfernen.

## SD Karte aktualisieren

Eine neue Version von RaspbianForStudentRobot kann ohne das Entfernen der SD Karte aus dem Raspberry Pi installiert werden. Die notwendigen Schritte werden hier beschrieben. Wen das Entfernen der SD Karte nicht stört kann alternativ den Schritten in *SD Karte initial beschreiben* folgen.

In der NOOBS Partition liegen die Installationsdateien für RaspbianForStudentRobot. Diese soll aktualisiert werden. Die Installation selber wird bei diesem Prozess nicht verändert. Erst beim nächsten Zurücksetzen der Installation werden die neuen Installationsdateien benutzt. NOOBS wird bei diesem Prozess nicht aktualisiert.

Als Quelle für das Image wird ein SMB Share angenommen.

```
sudo mkdir /mnt/transfer
sudo mount -r -t cifs -o user=<username> //<fileserver>/<folder> /mnt/transfer

sudo mkdir /mnt/noobs
sudo mount /dev/mmcblk0p1 /mnt/noobs

sudo rm -r /mnt/noobs/os/*

sudo unzip /mnt/transfer/<image>.zip os/* -x os/.placeholder -d /mnt/noobs/

sudo umount /mnt/transfer
sudo rmdir /mnt/transfer

sudo umount /mnt/noobs
sudo rmdir /mnt/noobs
```

Siehe Kapitel *Installation zurücksetzen* zum Installieren des neuen Images.

## Installation zurücksetzen

Die vorhandene Installation wird gelöscht und neu aufgesetzt. Alle gespeicherten Daten gehen dabei vorloren. Das ist hilfreich, wenn der Roboter von mehreren Personen genutzt wird und Änderungen des Vorgängers entfernt werden sollen, oder wenn eine neue Version installiert werden soll. Wichtige Dateien bitte vorher sichern.

Wird die u.g. Datei gelöscht, wird der NOOBS Installer beim Neustart automatisch das Image neu installieren und dann die Installation booten.

```
sudo rm /media/pi/SETTINGS/installed_os.json
sudo shutdown -r now
```

Die Zeitdauer für die Installation hängt von der Geschwindigkeit der SD Karte ab. Bei einer 32 GB Sandisk dauert die Installation etwa 15 Minuten. Der Vorgang ist abgeschlossen, wenn die Schreib LED (grün) aus bleibt.

Achtung beim ersten Verbinden: Hostname und Passwort wurden bei der Installation auch zurückgesetzt. Siehe Kapitel *Mit Roboter verbinden* für Voreinstellungen.

## Installation anpassen

TODO

```
sudo nano /etc/hostapd/hostapd.conf
```

Zeile *ssid* ändern.

```
ssid=student-robot1
```

```
sudo nano /etc/dnsmasq.conf
```

Zeile *address* ändern.

```
address=/student-robot1.home/192.168.42.1
```

```
sudo raspi-config
```

- Network Options > Hostname: *student-robot1*
- Finish, reboot

## SD Kartenimage erstellen

Wer sich nicht mit den Details der Installation herumschlagen möchte nimmt ein vorhandenes Kartenimage (siehe *SD Karte initial beschreiben*) und kann diesen Abschnitt ignorieren. :-)

### Kopieren von NOOBS und Raspbian auf die SD Karte

Die folgenden Schritte auf einem anderen Rechner als dem Raspberry Pi ausführen (z.B. einem Windows Laptop). Der Rechner muss auf die SD Karte schreiben können.

*NOOBS* (nicht *NOOBS Lite*) von [https://www.raspberrypi.org/downloads/noobs/](https://www.raspberrypi.org/downloads/noobs/) herunterladen, z.B. *NOOBS_v2_8_2.zip*.

SHA-256 kontrollieren.

Zip Datei entpacken. Der Inhalt wird in den nächsten Schritten modifiziert und dann auf eine SD Karte geschrieben.

Parameter ` silentinstall` an die Parameterliste in *recovery.cmdline* anhängen. Dieser Parameter wird für die initiale headless Installation und bei Updates benötigt. Ist bereits ein Betriebssystem installiert, wird NOOBS kein silentinstall durchführen. Damit kann der Parameter immer in der Datei bleiben.

Eine leere Datei *[ssh](files/ssh)* erstellen. Die Datei liegt im gleichen Verzeichnis wie *recovery.cmdline*. Die Datei wird beim Partitionsetup in die boot Partition kopiert und sorgt beim Boot Vorgang dafür, dass der ssh Server gestartet wird und man sich somit remote anmelden kann.

In Verzeichnis *os/* alle Betriebssysteme ausser *Raspbian* löschen (z.B. *LibreELEC_RPi*, *LibreELEC_RPi2*).

Eine große Datei *.placeholder* (Datei in [zip](files/placeholder1.5gb.zip)) in das Verzeichnis *os/* legen. Die Datei dient dazu, Platz in der ersten Partition zu reservieren. Dadurch können später auch größere Updates installiert werden.

microSD Karte mit mindestens 8 GB mit einer Partition und FAT32 formatieren.

Dateien auf die Karte kopieren.

Die lokalen Dateien behalten. Wir brauchen sie später bei der Erstellung des Images.

### Raspbian konfigurieren

SD Karte in den Raspberry Pi des GoPiGo3 stecken.

Ethernet Netzwerkkabel in den Raspberry Pi stecken.

Der Raspberry Pi/GoPiGo3 wird während der Softwareinstallation vorzugsweise über den USB Anschluss mit Strom versorgt. Die Akkus können entfernt werden.

Raspberry Pi anschalten (durch Einstecken des USB Kabels). Die Power LED des GoPiGo3 wird erst dann korrekt über An/Aus und Batteriezustand informieren, wenn die entsprechende Software installiert wurde.

Der Raspberry Pi installiert und bootet selbständig Raspbian. Die Zeitdauer für die Installation hängt von der Geschwindigkeit der SD Karte ab. Bei einer 32GB Sandisk dauert die Installation etwa 15 Minuten. Der Vorgang ist abgeschlossen, wenn die Schreib LED (grün) aus bleibt.

Netzwerkadresse ermitteln

Mit Raspberry Pi über ssh verbinden. Nutzername/Passwort sind *pi*/*raspberry*.

Passwort ändern.

```
passwd
```

*raspberry*, 2x *myr0bot*

Raspbian aktualisieren, reboot wenn notwendig.

```
sudo apt update
sudo apt upgrade
[ -f /var/run/reboot-required ] && sudo shutdown -r now
```

Konfiguration mit raspi-config

```
sudo raspi-config
```

- Network Options > Hostname: *student-robot*
- Boot Options > Desktop / CLI: Desktop Autologin
- Interfacing Options: enable Camera, VNC, SPI, I2C
- Finish, reboot

Samba installieren. Damit kann auf Verzeichnisse zugegriffen werden, und Windows Clients finden den Raspberry Pi mit dem Namen.

```
sudo apt install samba
```

Nutzer *pi* hinzufügen

```
sudo smbpasswd -a pi
```

2x *myr0bot*

Samba Konfiguration anpassen

```
sudo nano /etc/samba/smb.conf
```

Im Bereich *[homes]* folgende Parameter ändern:

*read only = yes* ändern in

```
   read only = no
```

*create mask = 0700* ändern in

```
   create mask = 0644
```

*directory mask = 0700* ändern in

```
   directory mask = 0755
```

Am Ende der Datei folgendes Share hinzufügen

```
[root]
   comment = root
   path = /
   read only = yes
   valid users = pi
```

Parameter überprüfen

```
testparm
```

Samba neu starten

```
sudo systemctl restart smbd
sudo systemctl restart nmbd
```

*ll* in der bash erlauben

```
nano .bashrc
```

Bei den *ls aliases* hinzufügen. Änderung gilt erst für die nächste bash session.

```
alias ll='ls -laF'
```

Midnight Commander (ein textbasierter Dateimanager) installieren.

```
sudo apt install mc
```

Feste Namen den Wi-Fi Adaptern zuweisen.

Nach dem Einstecken des USB WLAN Adapters hat der Raspberry Pi zwei WLAN Schnittstellen. Diese heissen *wlan0* und *wlan1*. Welche Schnittstelle welchen Namen bekommt ist zufällig und kann sich zwischen Neustarts ändern. Damit lässt sich kein Access Point aufsetzen oder Firewall Regeln definieren. Die *Predictable Network Interface Names* sind nur bedingt hilfreich. Beim Raspberry Pi bekommt der USB WLAN Adapter damit eine ID, die seine MAC Adresse beinhaltet. Das macht die Konfiguration aufwendiger, wenn das gleiche SD Kartenimage für mehrere Raspberries benutzt werden soll. Schlimmer noch: das interne WLAN ist manchmal wlan0, manchmal wlan1. Folgende Änderungen erzwingen den namen wlan0 für das interne WLAN und wlan1 für einen USB Adapter. Nur ein WLAN USB Adapter darf gleichzeitig benutzt werden.

Neue Datei anlegen

```
sudo nano /etc/udev/rules.d/72-wlan-geo-dependent.rules
```

Als Inhalt einfügen

```
#
# +---------------+
# | wlan1 | wlan1 |
# +-------+-------+
# | wlan1 | wlan1 |
# +---------------+ (RPI USB ports with position independent device names for a maximum of 1 optional wifi dongle)
# 
# | wlan0 | (onboard wifi)
#
ACTION=="add", SUBSYSTEM=="net", SUBSYSTEMS=="sdio", KERNELS=="mmc1:0001:1", NAME="wlan0"
ACTION=="add", SUBSYSTEM=="net", SUBSYSTEMS=="usb",  KERNELS=="1-1.2",       NAME="wlan1"
ACTION=="add", SUBSYSTEM=="net", SUBSYSTEMS=="usb",  KERNELS=="1-1.4",       NAME="wlan1"
ACTION=="add", SUBSYSTEM=="net", SUBSYSTEMS=="usb",  KERNELS=="1-1.3",       NAME="wlan1"
ACTION=="add", SUBSYSTEM=="net", SUBSYSTEMS=="usb",  KERNELS=="1-1.5",       NAME="wlan1"
```

Neu starten

```
sudo shutdown -r now
```

Zuweisung der Gerätenamen kontrollieren

```
ifconfig
```

*wlan0* sollte jetzt der interne WLAN Adapter sein, *wlan1* der USB Adapter, *eth0* das Ethernet Kabel und *lo* das Loopback Device.

### Access Point, DHCP und DNS Server installieren

Dnsmasq (DHCP und DNS Server) und hostapd (Access Point Software) installieren.

```
sudo apt-get install dnsmasq hostapd
```

Services stoppen, bis wir mit der Konfiguration fertig sind.

```
sudo systemctl stop dnsmasq
sudo systemctl stop hostapd
```

Der interne WLAN Adapter (*wlan0*) wird als Access Point genutzt. Ihm wird eine statische IP Adresse zugewiesen.

```
sudo nano /etc/dhcpcd.conf
```

Am Ende der Datei einfügen

```
interface wlan0
    static ip_address=192.168.42.1/24
```

Dhcpcd neu starten.

```
sudo systemctl restart dhcpcd
```

Dnsmasq konfigurieren

```
sudo nano /etc/dnsmasq.conf
```

Am Ende der Datei einfügen

```
interface=wlan0

dhcp-range=192.168.42.100,192.168.42.200,1h

no-hosts
address=/student-robot.home/192.168.42.1
```

Neue Konfigurationsdatei für hostapd erstellen

```
sudo nano /etc/hostapd/hostapd.conf
```

Als Inhalt einfügen

```
interface=wlan0
driver=nl80211
ssid=student-robot
hw_mode=g
#country_code=DE
# non-overlapping channels: 1, 6, 11
channel=1
ieee80211n=1
wmm_enabled=1
ht_capab=[HT40][SHORT-GI-20][DSSS_CCK-40]
macaddr_acl=0
auth_algs=1
ignore_broadcast_ssid=0
wpa=2
wpa_passphrase=changeitnow
wpa_key_mgmt=WPA-PSK
wpa_pairwise=TKIP
rsn_pairwise=CCMP
```

Position der Konfigurationsdatei festlegen

```
sudo nano /etc/default/hostapd
```

Zeile *#DAEMON_CONF=""* ändern in

```
DAEMON_CONF="/etc/hostapd/hostapd.conf"
```

Services starten

```
sudo systemctl start hostapd
sudo systemctl start dnsmasq
```

IP-Forwarding aktivieren

```
sudo nano /etc/sysctl.conf
```

Ändere Zeile *#net.ipv4.ip_forward=1* in

```
net.ipv4.ip_forward=1
```

Masquerate für ausgehende Verbindungen auf eth0 und wlan1.

```
sudo nano /etc/rc.local
```

Vor *exit 0* einfügen

```
iptables -t nat -A POSTROUTING -o eth0 -j MASQUERADE
iptables -t nat -A POSTROUTING -o wlan1 -j MASQUERADE
```

Wpa_supplicant soll nur wlan1 steuern (nicht aber den Access Point wlan0).

```
sudo mv /etc/wpa_supplicant/wpa_supplicant.conf /etc/wpa_supplicant/wpa_supplicant-wlan1.conf
```

Reboot

```
sudo shutdown -r now
```

### GoPiGo3 Software installieren

GoPiGo3 Software installieren und Reboot. Die Software beinhaltet u.a. einen Service für die GoPiGo3 Power LED und den Power Schalter, sowie Python Bibliotheken für GoPiGo3 Hardware.

```
curl -L https://dexterindustries.com/update_gopigo3 | bash
sudo shutdown -r now
```

DI_Sensors installieren - wird für den Abstandssensor benötigt.

```
curl -L https://dexterindustries.com/update_sensors | bash
```

### GoPiGo Scratch Erweiterung installieren

Die Erweiterung installieren.

```
git clone https://github.com/markokimpel/gopigoscratchextension.git ~/student-robot.org/gopigoscratchextension/
```

Zur Vorbereitung des Tests Raspberry Pi runterfahren. 

```
sudo shutdown -h now
```

Warten bis grüne LED nicht mehr leuchtet. Dann USB Stromversorgung entfernen.

Ethernetkabel entfernen.

### Installation testen

* Akku mit GoPiGo3 verbinden.
* GoPiGo3 über Power Taste starten. LED daneben sollte während des Ladens des Betriebssystems grün blinken. Dann sollte sie ständig grün leuchten.
* Laptop mit Access Point *student-robot*, passwort *changeitnow* verbinden.
* Der Laptop sollte eine IP Adresse im Bereich 192.168.42.100-200 erhalten haben.
* Mit *VNC Viewer* zu *student-robot.home* verbinden, Nutzer *pi*/*myr0bot*.
* Konfigurationstool mit Cancel abbrechen. Das Standardimage soll nicht auf eine spezielle Sprache oder Zeitzone eingestellt sein. Das kann bei *Installation anpassen* gemacht werden.
* Bildschirmauflösung auf 1280x720 ändern: Menü > *Preferences* > *Raspberry Pi Configuration*, *Set Resolution*, Neustart notwendig, evtl. erneut mit Access Point verbinden
* GoPiGo3 Verknüpfungen auf dem Desktop löschen. Die sind für die Integration mit Scratch 1 und verwirren deshalb eher.
* Bluetooth abschalten
* Adapter wlan1 mit lokalem WLAN verbinden.
* Öffentliche Webseite, z.B. [https://www.schueler-roboter.de/](https://www.schueler-roboter.de/), auf Laptop öffnen (bedeutet, dass IP Forwarding funktioniert).
* In Terminal: `cd ~/student-robot.org/gopigoscratchextension/gpg3server/`, `./run.sh`.
  * Sollte eine Fehlermeldung über zu alte Firmware erscheinen (*gopigo3.FirmwareVersionError: GoPiGo3 firmware needs to be version 1.0.x but is currently version 0.3.4*), dann aktuelle Firmware flashen: `cd ~/Dexter/GoPiGo3/`, `sudo bash Firmware/gopigo3_flash_firmware.sh`.
* Scratch 2 starten: Menü *Programming* > *Scratch 2*
* Beispielprogramm *~/student-robot.org/gopigoscratchextension/scratch_examples/Simple Manual Rover.sb2* öffnen
* Experimentelle Erweiterung laden: *http://student-robot.home:8080/scratch_extension.js* (mit Umschalt + linke Maustaste auf *File* Menü)
* Bewegungen testen
* Abstandssensor testen (Doppelklick auf *distance* Block)
* In weiterem Terminal: `cd ~/student-robot.org/gopigoscratchextension/streamingserver/`, `./run.sh`
* Video in Browser testen: http://student-robot.home:8081/
* Beide Server stoppen
* Zugriff auf Samba Shares. Nutzer *pi*/*myr0bot*. Share *\\\\student-robot.home\\root* sollte nur lesbar sein, *\\\\student-robot.home\\pi* sollte auch schreibbar sein.
* Zugangsdaten zum lokalen Netzwerk löschen damit sie nicht im image auftauchen: `sudo nano /etc/wpa_supplicant/wpa_supplicant-wlan1.conf`, die beiden ersten Zeilen bleiben stehen.
* GoPiGo3 über Power Taste herunterfahren. Während des Herunterfahrens blinkt sie rot, dann geht sie aus.

### Partitionen sichern

Ethernetkabel mit Raspberry Pi verbinden.

Stromversorgung vorzugsweise über USB Port. Die Akkus können entfernt werden.

Nicht benötigte Pakete entfernen, ggf. Reboot.

```
sudo apt autoremove
[ -f /var/run/reboot-required ] && sudo shutdown -r now
```

Die Partitionen werden mit *bsdtar* gesichert.

```
sudo apt install bsdtar
```

Die Archive müssen ausserhalb der zu sichernden Partition gespeichert werden, z.B. auf einem SMB Share.

```
sudo mkdir /mnt/transfer
sudo mount -t cifs -o user=<username> //<fileserver>/<folder> /mnt/transfer
```

Boot Partition mit bsdtar sichern.

Die Datei *cmdline.txt* beziehen wir vom Originalarchiv in der NOOBS Partition. Sie wurde während der Installation verändert. Die Datei *os_config.json* wird während der Installation erzeugt und muss deshalb nicht gesichert werden. Die Datei *config.txt* enthält Informationen zur Aktivierung der Kamera, der Schnittstellen SPI und I2C, sowie die voreingestellt Bildschirmauflösung.

```
sudo bsdtar --numeric-owner --format gnutar -cpvf /mnt/transfer/boot.tar -C /boot --exclude ./cmdline.txt --exclude ./os_config.json .

sudo mkdir /mnt/noobs
sudo mount -r /dev/mmcblk0p1 /mnt/noobs

cd ~
cp /mnt/noobs/os/Raspbian/boot.tar.xz boot.tar.xz
unxz boot.tar.xz
sudo bsdtar --numeric-owner --format gnutar -rpvf /mnt/transfer/boot.tar --include ./cmdline.txt @boot.tar
rm boot.tar

sudo umount /mnt/noobs
sudo rmdir /mnt/noobs
```

Root Partition mit bsdtar sichern.

```
sudo bsdtar --numeric-owner --format gnutar --one-file-system -cpvf /mnt/transfer/root.tar -C / .
```

TODO: Dateien/Verzeichnisse ausschliessen

Während der Ausführung von bsdtar in der Root Partition werden die folgenden Fehlermeldungen auf stderr ausgegeben. Sie können ignoriert werden.
* Viele Male *: tar format cannot archive socket*: diese Fehlermeldung bezieht sich auf Sockets im Verzeichnis /var/lib/samba/private/msg.sock/
* *bsdtar: Couldn't list extended attributes: No data available*: diese Fehlermeldung bezieht sich auf das Verzeichnis /media/pi/

Das SMB Share wieder entfernen.

```
sudo umount /mnt/transfer
sudo rmdir /mnt/transfer
```

Das Komprimieren geht am schnellsten, wenn eine schnelle CPU mit mehreren Kernen und viel Speicher zur Verfügung stehen. Das geht ausserhalb des Raspberry Pis am besten. Neuere Versionen von *xz* unterstützen die Option `-T 0`. Damit werden mehrere Ausführungs-Threads genutzt.

```
xz -k -9 -e -T 0 boot.tar
xz -k -9 -e -T 0 root.tar
```

### Partitionen in NOOBS integrieren

Jetzt wird das ausgepackte NOOBS Image aus dem ersten Schritt weiter modifiziert.

Verzeichnis *os/Raspbian/* in *os/RaspbianForStudentRobot/* umbenennen.

Die folgenden Änderungen erfolgen im Verzeichnis *os/RaspbianForStudentRobot/*.

Beim Editieren von Textdateien auf Unix Zeilenendungen achten.

Datei *os.json* anpassen. Neuer Inhalt:

```
{
    "description": "Raspbian with modifications for the Student-Robot",
    "kernel": "4.14",
    "name": "RaspbianForStudentRobot",
    "password": "myr0bot",
    "release_date": "2018-08-15",
    "supported_models": [
        "Pi 3"
    ],
    "url": "https://www.student-robot.org/",
    "username": "pi",
    "version": "stretch"
}
```

In Datei *partitions.json* for partition *root* folgende Werte anpassen:

* *uncompressed_tarball_size*: Größe in MB (1 MB = 1.000.000 Byte), z.B. `4354`
* *partition_size_nominal*: mindestens 400 MB mehr, z.B. `5000`

Datei *Raspbian.png* in *RaspbianForStudentRobot.png* umbenennen.

Datei *[README.txt](files/README.txt)* dem Verzeichnis hinzufügen.

Datei *boot.tar.xz* durch die oben erzeugte Version ersetzen.
Datei *root.tar.xz* durch die oben erzeugte Version ersetzen.

Das gesamte NOOBS Verzeichnis in ein zip, z.B. *RaspbianForStudentRobot_2018-08-15.zip*, einpacken. Dateien wie *recovery.cmdline* liegen direkt im Wurzelverzeichnis.

Glückwunsch, du hast ein neues SD Kartenimage erzeugt. Dieses kann nun wie in *SD Karte initial beschreiben* und *SD Karte aktualisieren* beschrieben genutzt werden.

## Referenzen

* [https://github.com/raspberrypi/noobs](https://github.com/raspberrypi/noobs)
* [https://www.raspberrypi.org/forums/viewtopic.php?t=198946](https://www.raspberrypi.org/forums/viewtopic.php?t=198946)
* [https://www.raspberrypi.org/documentation/configuration/wireless/access-point.md](https://www.raspberrypi.org/documentation/configuration/wireless/access-point.md)
* [https://w1.fi/cgit/hostap/plain/hostapd/hostapd.conf](https://w1.fi/cgit/hostap/plain/hostapd/hostapd.conf)
* [https://github.com/DexterInd/GoPiGo3](https://github.com/DexterInd/GoPiGo3)
* [https://github.com/DexterInd/DI_Sensors](https://github.com/DexterInd/DI_Sensors)

*Copyright 2018 Marko Kimpel*

*Licensed under the GNU General Public License version 3, or (at your option) any later version.*

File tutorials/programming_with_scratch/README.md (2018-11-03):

---
title: Programmieren mit Scratch
permalink: /tutorials/programming_with_scratch/
breadcrumb_path: home
show_toc: true
---

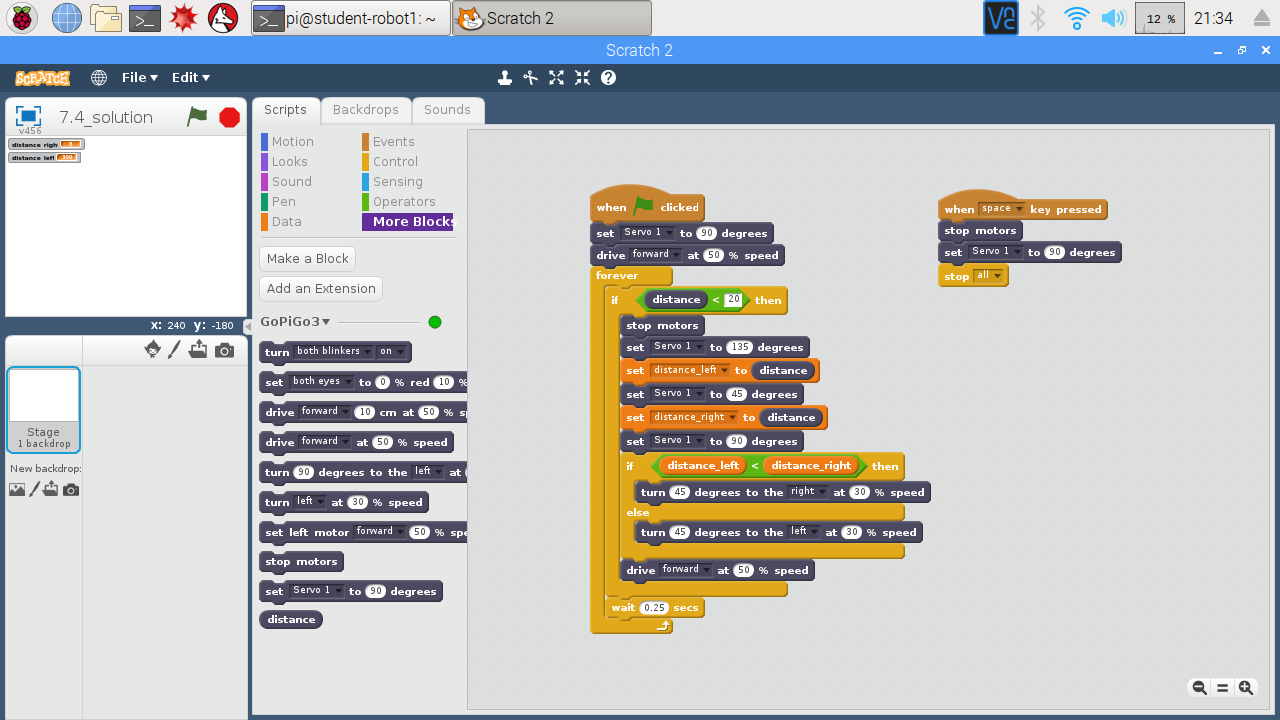
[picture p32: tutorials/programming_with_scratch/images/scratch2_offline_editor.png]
Scratch 2 Offline Editor

Scratch 2 Offline Editor

## Voraussetzungen

* Roboter mit der aktuellen Software (siehe [Bau des Roboters](../build_a_robot/) und [Basisinstallation Software](../software_image/))
* Einen weiteren Computer um auf den Roboter zuzugreifen. An diesem Computer sitzt du und programmierst den Roboter. Der Computer kann ein Raspberry Pi mit Monitor, Tastatur und Maus sein, oder ein Windows Laptop. Da der Roboter über WLAN kommuniziert, muss auch der weitere Computer über WLAN kommunizieren können.
* Wie du den Roboter an- und ausschaltest und dich mit dem VNC Viewer verbindest ist in [Basisinstallation Software](../software_image/) Kapiteln *Mit Roboter verbinden* und *Roboter ausschalten* erklärt.

## GoPiGo3 Server starten

* Scratch benötigt eine Erweiterung um den Roboter steuern zu können. Teil der Erweiterung ist der GoPiGo3 Server. Dieser muss zuerst gestartet werden.
* Terminal öffnen und ausführen

```
pi@student-robot:~ $ cd gopigoscratchextension/
pi@student-robot:~/gopigoscratchextension $ cd gpg3server/
pi@student-robot:~/gopigoscratchextension/gpg3server $ ./run.sh 
Server listening at 0.0.0.0:8080

GPG3 Server homepage : http://127.0.0.1:8080/
Scratch extension URL: http://127.0.0.1:8080/scratch_extension.js

Press Ctrl-C to stop server
```

* Sollte beim Starten des Serves eine Fehlermeldung über zu alte Firmware erscheinen (z.B. *gopigo3.FirmwareVersionError: GoPiGo3 firmware needs to be version 1.0.x but is currently version 0.3.4*), dann muss die GoPiGo3 Firmware einmalig aktualisiert werden:

```
pi@student-robot:~ $ cd ~/Dexter/GoPiGo3/
pi@student-robot:~/Dexter/GoPiGo3 $ sudo bash Firmware/gopigo3_flash_firmware.sh
```

* Bitte die angezeigten URLs für *GPG3 Server homepage* und *Scratch extension URL* beachten. Diese werden später gebraucht.
* Bitte das Terminal offen lassen, während man mit Scratch arbeitet. Das Schliessen des Terminals würde den Server stoppen.

## Roboterfunktionen kennen lernen

* Im Browser die GPG3 Server homepage (im Beispiel *http://127.0.0.1:8080/*) öffnen.
* Zu *Controller UI* gehen.

## Scratch starten

* Scratch ist Teil der Rasbian Distribution und damit Teil des Schüler-Roboter Images.
* Menüpunkt *Programming*, *Scratch 2* starten
* Die Sprache kann bei Bedarf geändert werden. Hierzu den Erdball links oben anklicken und die gewünschte Sprache wählen. Viele Texte, aber nicht alle, erscheinen dann in der gewählten Sprache.
* Das Laden von Erweiterungen funktioniert in Scratch 2 so:
  * Umschalttaste (Shift-Taste) gedrückt halten und Menü *Datei* anklicken.
  * Durch das Drücken der Umschalttaste werden weitere Menüpunkte angezeigt. Wir wählen *Import experimental extension*.
  * Die *Scratch extension URL* (im Beispiel *http://127.0.0.1:8080/scratch_extension.js*) eingeben.
  * Im Bereich *Skripte* werden in der Gruppe *Weitere Blöcke* Funktionen angeboten, die du zum Steuern des Roboters benutzen kannst.
  
## Projekte laden und speichern in Scratch

* Das Laden und Speichern von Projekten mit Erweiterungen ist etwas hakelig in Scratch 2. Wird in einem Projekt eine Erweiterung verwendet, so verwendet Scratch beim Speichern des Projekts immer den Dateiendung *.sbx* (auch wenn man eine andere angibt). Beim Laden besteht Scratch jedoch auf die Dateiendung *.sb2*.
* Ein Workaround ist, die Projekte mit *.sbx* Dateinamen zu speichern und einen Link vom *.sb2* Dateinamen auf den *.sbx* Dateinamen zu erstellen. Damit steht der Inhalt der Datei unter zwei verschiedenen Dateinamen zur Verfügung. Bei Laden des Projektes wählt man dann einfach den *.sb2* Dateinamen und läd somit den Inhalt der *.sbx* Datei.
* Im Terminal:

```
pi@student-robot:~/Scratch $ ls -l
total 60
-rw------- 1 pi pi 58064 Apr 15 13:53 Project.sbx
pi@student-robot:~/Scratch $ ln -s Project.sbx Project.sb2
pi@student-robot:~/Scratch $ ls -l
total 60
lrwxrwxrwx 1 pi pi    11 Apr 15 13:58 Project.sb2 -> Project.sbx
-rw------- 1 pi pi 58064 Apr 15 13:53 Project.sbx
pi@student-robot:~/Scratch $ 
```

* Nach dem Laden des Projektes erscheinen Blöcke aus der Erweiterung rot. Lade nun die Erweiterung wie oben beschrieben. Die Blöcke erscheinen dann grau und können benutzt werden.

## Übung 1: Blinken

### Programmiertechniken

* Sequenz
* Schleife

### Aufgabe 1.1

* Blinke 2x mit beiden Blinkern
* Blinken: Blinker LED an für eine Zeitspanne, dann Blinker LED aus für eine Zeitspanne.
* Finde einen geeigneten Block in der Gruppe *Weitere Blöcke* zur Steuerung.
* Nutze den *warte* Block aus der Gruppe *Steuerung*. Tipp: Nutze die englische Notation (Punkt statt Komma) bei der Eingabe eines Bruchteils einer Sekunde (z.B. *0.5*).
* Finde eine geeignete Zeitdauer für das Blinken.

*Beispiellösung*

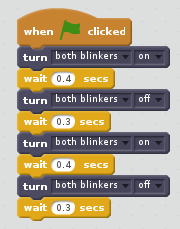
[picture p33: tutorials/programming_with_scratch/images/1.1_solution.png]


[1.1_solution.sbx](scratch/1.1_solution.sbx)

### Aufgabe 1.2

* Blinke 10x mit beiden Blinkern
* Suche einen gegeigneten Block in der Gruppe *Steuerung* um ein *schönes* Programm zu schreiben.
* Warum ist das Programm mit einer Schleife *schöner*?

*Beispiellösung* 

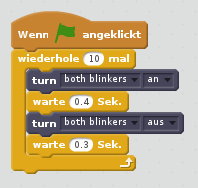
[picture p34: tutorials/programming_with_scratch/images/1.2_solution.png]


[1.2_solution.sbx](scratch/1.2_solution.sbx)

## Übung 2: Musterfahrt

### Programmiertechniken

* Sequenz
* Schleife

### Aufgabe 2.1

* Lass deinen Roboter folgendes Muster fahren.

```
+------+
|      |
|      |
|      |
^------+
```

* Kantenlänge ist jeweils 30 cm.
* Am Ende soll der Roboter auf der Ausgangsposition stehen und in die gleiche Richtung schauen.
* Kann das Programm mit einer Schleife vereinfacht werden?

*Beispiellösung*

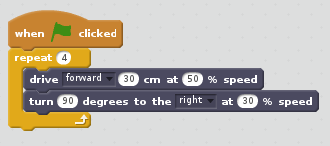
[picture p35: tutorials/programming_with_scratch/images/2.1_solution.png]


[2.1_solution.sbx](scratch/2.1_solution.sbx)

### Aufgabe 2.2

* Lass deinen Roboter folgendes Muster fahren.

```
^----+
     |
     |
+----+
|
|
+----+
     |
     |
+----+
|
|
^
```

* Kantenlänge ist jeweils 30 cm.
* Kann das Programm mit einer Schleife vereinfacht werden?

*Beispiellösung*

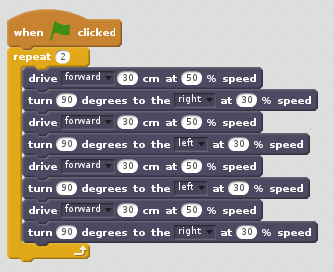
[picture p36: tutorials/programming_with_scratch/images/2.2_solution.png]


[2.2_solution.sbx](scratch/2.2_solution.sbx)

## Übung 3: Warnlichter beim Fahren

### Programmiertechniken

* Sequenz
* Schleife
* Parallelisierung

### Aufgabe 3.1

* Viele große Fahrzeuge nutzen Warntöne oder Warnlichter um ihrer Umgebung anzuzeigen, dass sie sich bewegen.
* Nutze die Augen des Roboters als Warnlicht. Es soll regelmäßig kurz rot aufblitzen.
* Die Warnlichter sollen beginnen zu blitzen, wenn das Programm startet (Nutzer klickt grünes Fähnchen) und aufhören, wenn es endet (Nutzer klickt rotes Stopp-Symbol).
* Der Roboter bewegt sich in dieser Aufgabe noch nicht.

*Beispiellösung*

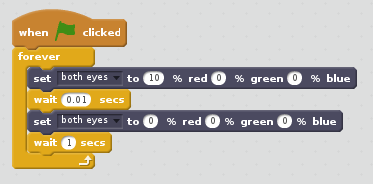
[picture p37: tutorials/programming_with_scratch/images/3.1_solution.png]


[3.1_solution.sbx](scratch/3.1_solution.sbx)

### Aufgabe 3.2

* Füge dem Projekt ein weiteres Script - mit eigenem *wenn grüne Fahne angeklickt* Startblock - hinzu. Das Script soll die aus Aufgabe 2.1 bekannte Aufgabenstellung - ein Quadrat abfahren - lösen.
* Führe das Projekt aus. Was stellst du fest?

*Beispiellösung*

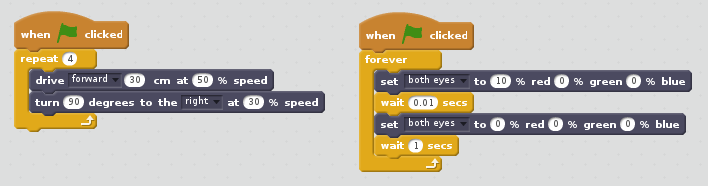
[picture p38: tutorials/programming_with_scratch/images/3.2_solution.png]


[3.2_solution.sbx](scratch/3.2_solution.sbx)

Beobachtung:
* Scripte zum Fahren und Blitzen werden gleichzeitig ausgeführt.
* Wenn das Script zum Fahren endet, läuft das Script zum Blitzen weiter - bis das Programm gestoppt wird.
* Das Blitzscript müsste automatisch gestoppt werden, wenn das Fahrscript endet.

### Aufgabe 3.3

* In der Gruppe *Steuerung* gibt es einen Block zum Stoppen von Scripten.
* Nutze diesen Block so, dass am Ende der Fahrtstrecke das Warnlicht abgeschaltet wird.

*Beispiellösung*

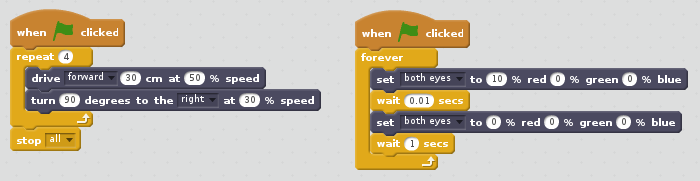
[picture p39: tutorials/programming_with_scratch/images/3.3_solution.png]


[3.3_solution.sbx](scratch/3.3_solution.sbx)

## Übung 4: Manuelle Robotersteuerung

### Programmiertechniken

* Ereignisorientierung
* Verzweigung
* Variablen
* Unterprogramme

### Aufgabe 4.1

* Der Roboter soll über die Richtungstasten (Pfeil nach oben, unten, links, rechts) gesteuert werden. Die Leertaste soll den Roboter anhalten. Wird eine Richtungstaste gedrückt, bewegt sich der Roboter solange in diese Richtung, bis eine andere Richtung, oder Stopp gewählt wird.
* Nutze den *Wenn Taste gedrückt* Block aus der Gruppe *Ereignisse*.
* Der Roboter soll sich langsam bewegen: vorwärts/rückwärts bei 50% Geschwindigkeit, links/rechts bei 30% Geschwindigkeit.
* Tipp: Implementiere zuerst die Stopp-Taste. :-)

*Beispiellösung*

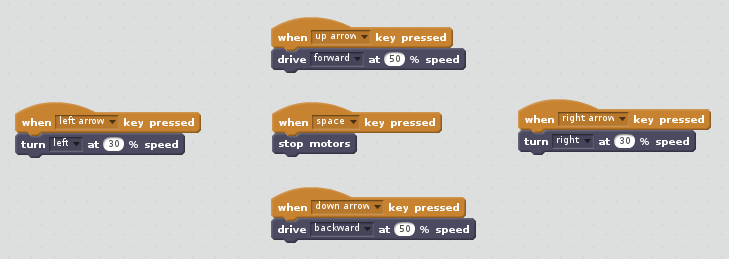
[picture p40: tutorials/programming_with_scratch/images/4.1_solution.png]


[4.1_solution.sbx](scratch/4.1_solution.sbx)

### Aufgabe 4.2

* Erlaube dem Roboter mit unterschiedlichen Geschwindigkeiten vorwärts und rückwärts zu fahren.
* Zur Steuerung werden die Tasten Pfeil nach oben und Pfeil nach unten benutzt. Beim Drücken der Pfeil nach oben Taste wird die Geschwindigkeit beim Vorwärtsfahren erhöht bzw. die Geschwindigkeit beim Rückwärtsfahren reduziert. Beispiele: Roboter steht, 1x Pfeil nach oben -> 50% vorwärts, nochmaliges Drücken -> 100% vorwärts. Die Pfeil nach unten Taste reduziert die Geschwindigkeit beim Vorwärtsfahren und erhöht die Geschwindigkeit beim Rückwärtsfahren. Beispiele: Roboter fährt mit 100% vorwärts, 1x Pfeil nach unten -> 50% vorwärts, nochmaliges Drücken -> Stopp, nochmaliges Drücken -> 50% rückwärts, nochmaliges Drücken -> 100% rückwärts.
* Benutze eine Variable um dir die gewählte Vorwärts/Rückwärts-Geschwindigkeit zu merken. Variablen findest du in der Gruppe *Daten* in Scratch.

*Beispiellösung*

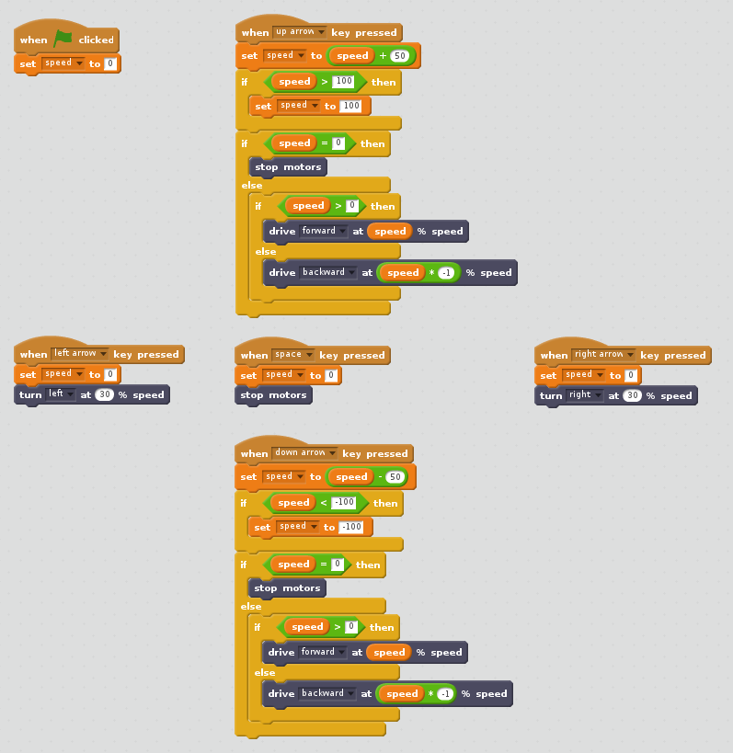
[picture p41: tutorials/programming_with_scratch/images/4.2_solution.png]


[4.2_solution.sbx](scratch/4.2_solution.sbx)

### Aufgabe 4.3

* Enthalten mehrere Scripte den gleichen Programmcode, kann es sinnvoll sein, diesen in einen weiteren Block zu verschieben und von verschiedenen Stellen her aufzurufen.
* Definiere einen neuen Block in der Gruppe *Weitere Blöcke*. Dieser Block die zum Vorwärts-/Rückwärtsfahren notwendigen Schritte enthalten.

*Beispiellösung*

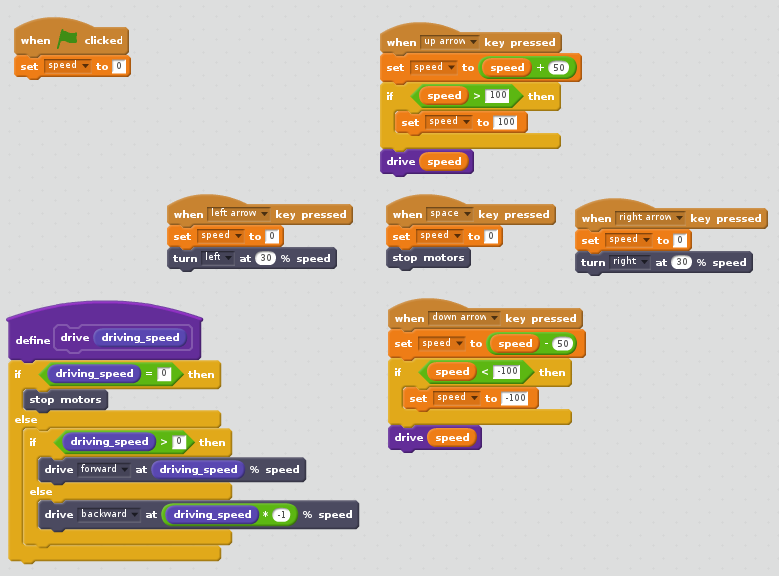
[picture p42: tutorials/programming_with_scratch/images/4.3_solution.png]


[4.3_solution.sbx](scratch/4.3_solution.sbx)

## Übung 5: Blinken beim Abbiegen

### Programmiertechniken

* Ereignisorientierung
* Nachrichten
* Klassen
* Parallelisierung

### Aufgabe 5.1

* Die manuelle Robotersteuerung aus Übung 4 soll um die Funktion des Blinkens erweitert werden. Als Blinker werden die roten LEDs an der Vorderseite des GoPiGo3 genutzt.
* Über die Tasten *S* und *D* soll der linke bzw. rechte Blinker aktiviert werden. Nach der Aktivierung blinkt er regelmäßig, bis ein anderer Blinker oder die Taste *X* gedrückt wird. Taste X schaltet die Blinker ab.
* Die Blinkfunktion soll über eine weitere Figur realisiert werden, die auf die Nachrichten *flash_left_blinker*, *flash_right_blinker* und *stop_blinkers* reagiert. Diese Nachrichten werden jeweils bei Druck der Tasten S, D und X gesendet.

*Beispiellösung*

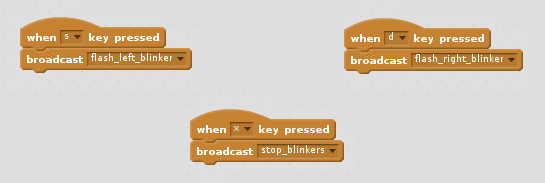
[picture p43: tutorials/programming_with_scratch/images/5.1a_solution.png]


Neue Figure *Blinker*:

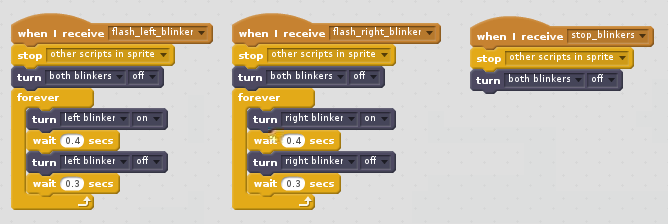
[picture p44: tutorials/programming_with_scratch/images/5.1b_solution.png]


[5.1_solution.sbx](scratch/5.1_solution.sbx)

- Beim Drücken der Tasten S oder D wird eine Nachricht gesendet und nicht auf deren Verarbeitungsende gewartet (asynchrone Verarbeitung). Damit wird ein neuer Ausführungspfad (Thread) für den Empfänger der Nachricht gestartet.
- Der Ausführungspfad ist realisiert als Endlosschleife, die den jeweiligen Blinker regelmäßig an und aus schaltet. Die Endlosschleife wird durch den Block *Stoppe andere Skripte der Figur* durch ein anders Skript der Figur.

### Aufgabe 5.2

* Die Blinker sollen nicht nur manuell ausgeschaltet werden können, sondern gehen automatisch aus, wenn nach der Kurvenfahrt wieder in die Geradeausfahrt gewechselt wird.

*Beispiellösung*

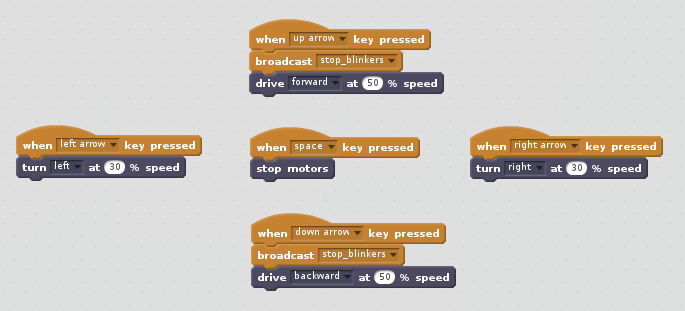
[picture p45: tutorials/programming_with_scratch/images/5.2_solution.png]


[5.2_solution.sbx](scratch/5.2_solution.sbx)

## Übung 6: Geschwindigkeitsmessung

### Programmiertechniken

* Schleife
* Verzweigung
* Variablen

### Aufgabe 6.1

* Der Roboter hat einen Abstandssensor. Nutze ihn um die Geschwindigkeit eines ihm entgegenkommenden Objekts zu ermitteln.
* Die Geschwindigkeit soll in cm/s und km/h angezeigt werden.
* Idee: Es werden zwei Abstandsmessungen durchgeführt. Zu jeder Messung wird die Zeit mit Hilfe der *Stoppuhr* ermittelt. Aus dem Abstandsunterschied und der dafür benötigten Zeitdauer wird die Geschwindigkeit errechnet.

*Beispiellösung*

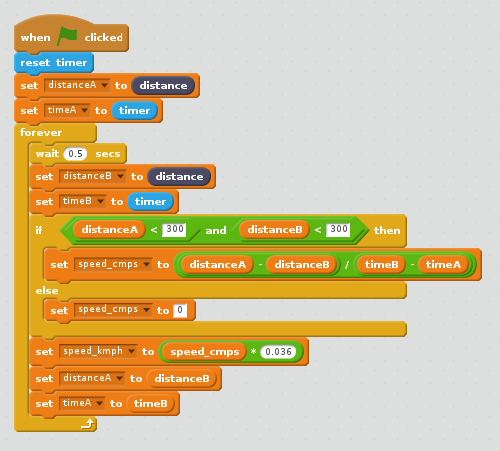
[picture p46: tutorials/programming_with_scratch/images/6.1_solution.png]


[6.1_solution.sbx](scratch/6.1_solution.sbx)

## Übung 7: Hindernisvermeidung

### Programmiertechniken

* Schleife
* Verzweigung
* Variablen

### Aufgabe 7.1

* In dieser Übung soll der Roboter lernen, sich selbständig in seiner Umgebung zu bewegen - ohne anzustossen. Wir beginnen einfach und erweitern das Programm schrittweise.
* Nach Programmstart soll der Roboter geradeaus fahren, bis er in ca. 20 cm Entfernung ein Hindernis erkennt. Da soll er stehen bleiben und das Programm endet.
* Tipp: Schreibe auch ein Skript um den Roboter im Notfall mit einem Tastendruck stoppen zu können - eine Art *Notaus*.

*Beispiellösung*

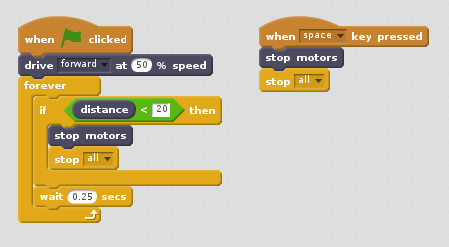
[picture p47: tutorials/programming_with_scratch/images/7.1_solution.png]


[7.1_solution.sbx](scratch/7.1_solution.sbx)

### Aufgabe 7.2

* Der Roboter soll vor Hindernissen so lange stehen bleiben, bis diese sich wegbewegen (z.B. ein Mensch). Ist das Hindernis mindestens 30 cm vom Roboter entfernt, setzt er seine Fahrt fort. Bis er wieder auf ein Hindernis trifft...

*Beispiellösung*

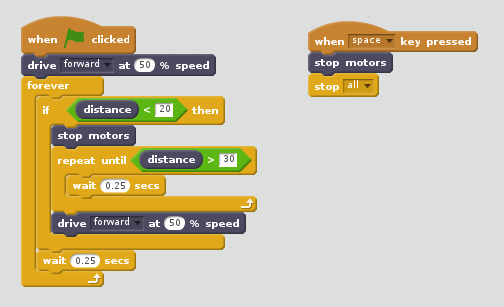
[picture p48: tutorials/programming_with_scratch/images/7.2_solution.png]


[7.2_solution.sbx](scratch/7.2_solution.sbx)

### Aufgabe 7.3

* Statt vor dem Hindernis stehen zu bleiben und zu warten, soll sich der Roboter langsam auf der Stelle drehen und damit eine freie Bahn suchen. Ist mehr als 30 cm Platz setzt er seine Fahrt fort. Er ist dem Hindernis ausgewichen.

*Beispiellösung*

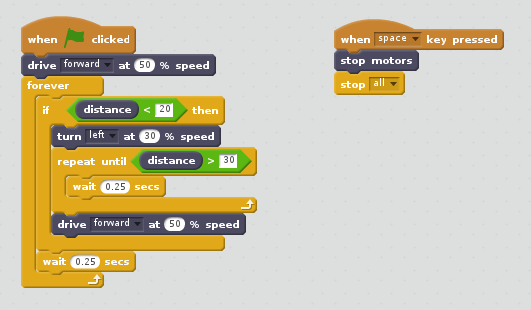
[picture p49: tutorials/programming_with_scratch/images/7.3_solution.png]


[7.3_solution.sbx](scratch/7.3_solution.sbx)

### Aufgabe 7.4

* Stösst der Roboter auf ein Hindernis, soll er den Servo Motor nutzen, um den Freiraum rechts und links von ihm zu ermitteln. In die Richtung, wo der meiste Platz ist, soll er seine Fahrt fortsetzen. 

*Beispiellösung*

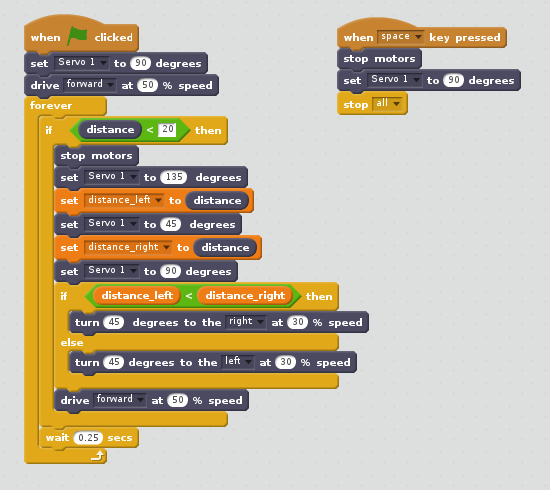
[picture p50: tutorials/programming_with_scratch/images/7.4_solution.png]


[7.4_solution.sbx](scratch/7.4_solution.sbx)

## Genutzte Programmiertechniken

* Sequenz
* Verzweigung
* Schleife
* Ereignisorientierung
* Parallelisierung
* Nachrichten
* Variablen 
* Unterprogramme
* Klassen

## Ideen für Erweiterungen

* Übung X: Ladar Screen
* Übung X: IFR Approach
* Übung X: Kamera
* Übung X: Durch Labyrinth fahren
* Script zum erstellen von .sb2 links für .sbx Dateien

*Copyright 2018 Marko Kimpel*

*Licensed under the GNU General Public License version 3, or (at your option) any later version.*

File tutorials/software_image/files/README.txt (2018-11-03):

'Raspbian for Student Robot' is a modified Raspbian install for the
Student-Robot project (see https://www.student-robot.org/).

The install uses software from many upstream projects, so there are many
copyright owners. The project makes NO claim of copyright on any upstream
software. Please review the instructions how the install was created at
https://www.schueler-roboter.de/tutorials/create_sr_image/ to learn about
used software and to review their licenses.

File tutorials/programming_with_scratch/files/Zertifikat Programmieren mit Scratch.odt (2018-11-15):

Schüler-Roboter

Der programmierbare Roboter für Schüler jeden Alters

www.schueler-roboter.de

Workshop „Programmieren mit Scratch“

Teilnehmer: __________________________________________________

Datum: _________________

Diese Programmiertechniken habe ich genutzt:

Sequenz | Verzweigung | Schleife
Ereignisorientierung | Parallelisierung | Nachrichten
Variablen | Unterprogramme | Klassen

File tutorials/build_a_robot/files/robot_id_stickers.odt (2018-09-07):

Wi-Fi: student-robot1

①

①

①

Host: student-robot1.home

User: pi

②

②

Wi-Fi: student-robot2

②

Host: student-robot2.home

User: pi

③

③

Wi-Fi: student-robot3

③

Host: student-robot3.home

User: pi

④

④

Wi-Fi: student-robot4

④

Host: student-robot4.home

User: pi

⑤

⑤

Wi-Fi: student-robot5

⑤

Host: student-robot5.home

User: pi

⑥

⑥

Wi-Fi: student-robot6

⑥

Host: student-robot6.home

User: pi

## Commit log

2017-11-19 Markokimpel dedicated schüler roboter.de repo (#1)
    * Delete README.md
    * Rename de/README.md to README.md
    * Rename de/project/README.md to project/README.md
2018-01-29 added basic information about version 1 of hardware
    * added images and 3d model files
    * show version 1 on homepage
    * slight changes to structure on homepage
    [SR1 Base Plate Rev 3.stl, SR1 Cage Rev 0.stl, SR1 Motor Bracket L Rev 4.stl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]
2018-01-29 added link to RasPiRobot Board Scratch Extension
2018-05-05 added trailing slashes to folder names
    Currently each URL to a folder results in two 302 redirects, e.g. https://www.schueler-roboter.de/contact -> http://www.schueler-roboter.de/contact/ -> https://www.schueler-roboter.de/contact/. The hope is that using trailing slashes in the markup will avoid these redirects.
2018-05-05 3 neue Übungen in der Scratch Anleitung
2018-10-01 consolidated instructions, firmware flash, minor changes
    - added instructions on how to flash GoPiGo3 firmware
    - deferred to create_sr_image for instructions how to power on and off robot and how to connect
    - minor changes
2022-12-09 switch from Universal Analytics (UA) to Google Analytics 4 (GA4)
